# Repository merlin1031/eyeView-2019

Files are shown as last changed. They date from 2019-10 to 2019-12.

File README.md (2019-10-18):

# eyeView-2019 FPV Twin-Mot Plane
eyeView2019 ist ein aus 5mm Depron gebauter, 2-motoriger FPV-Hochdecker der mit 5,8GHz Video-Übertragung den FPV-Flug ermöglicht.
Bei der Konstruktion von eyeView wurde besonders darauf geachtet, dass zu Ausbildungszecken im Bereich CAD möglichst viele Aspekte des eingesetzten CAD-Systems SolidWorks 2019 angewendet werden. Die einzelnen Bauteile werden im Laufe des Projektes dann auf einem LaserCutter und auf einem 3D-Drucker erstellt.

## Idee und Konzept
Angetrieben wird eyeView2019 durch zwei Micro-Brushless-Motoren der FPV-Racer-Drohen Szene. I.d.R. bestiten diese Motoren genügend Kraft um ca. 2KG Schub produzieren zu können. Das dürfte dann bei einem minimalen Abfluggewicht von ca. 500g bis 700g für ein Schubverhälnis von min 1:2 oder noch besser 1:3 sorgen. Zudem sind diese Motoren aktuell zu sehr günstigen Preise überall in den verschiedensten Ausführungen verfügbar.
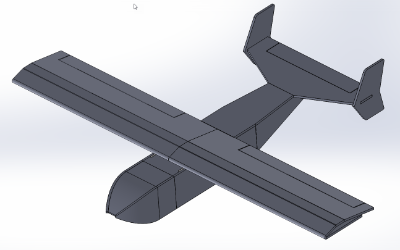
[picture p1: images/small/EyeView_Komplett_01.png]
eyeView2019 - Gesammtansicht Zwischenstand

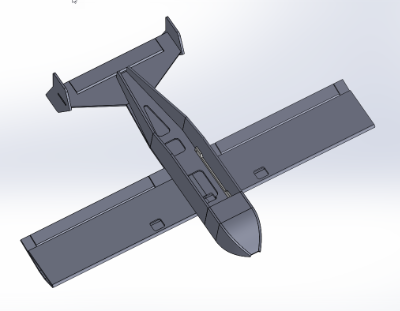
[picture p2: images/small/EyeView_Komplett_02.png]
eyeView2019 - Gesammtansicht Zwischenstand


Die Tragfläche besteht aus insgesamt 4 Einzelteilen, die bei der Montage übergangsweise mit Klebeband zusammengeklebt werden, damit die einzelnen Bauteile zueinander ihre Posisitonierung behalten. Verklebt werden die Deproonteile mit PUR-Leim, der eine Aushärtungszeit von ca. 24h besitzt. Der Vorteil beim Einsatz von PUR-Leim besteht darin, dass dieser mit Hilfe von Feuchtigkeit aufschäumt und somit kleinere Spalte überbrückt. Bei der Verarbeitung von PUR-Leim sind die entsprechenden Sicherheits-Vorschriften einzuhalten.
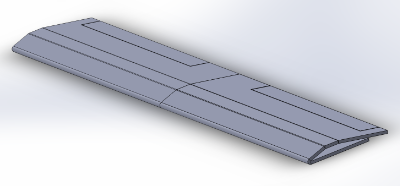
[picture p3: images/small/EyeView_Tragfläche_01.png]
eyeView2019 - Tragfläche


Die Rumpfnase besteht auf vier einzelnen Depron-Platten die leicht über einer Kante in Formbebracht werden. Durch die Formgebung ergibt sich dann eine recht aerodynamische Rumpfnase bei geringem Gewicht. Die Kamera-Halterung für die FPV Kamera wird aus einem 3D gedruckten PLA-Teil bestehen, das in die Rumpfnase aus Depron eingeklebt wird und somit der Kamera etwas mehr Schutz bei einem Crash bietet als reines Depron.
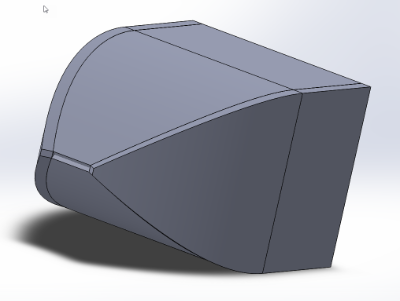
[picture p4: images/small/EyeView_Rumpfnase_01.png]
eyeView2019 - Rumpfnase als Oberflächenteil


## Komponenten und Bauteile
### Rumpf
muss noch beschrieben werden

### Tragfläche

### Höhenleitwerk

### Rumpfnase

### Motor-Gondeln

## weitere Infos

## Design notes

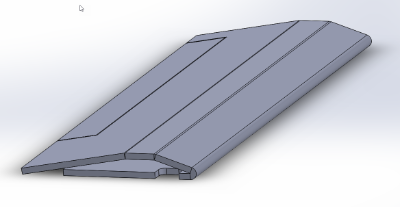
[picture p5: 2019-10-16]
images/small/EyeView_Tragfläche_03.png

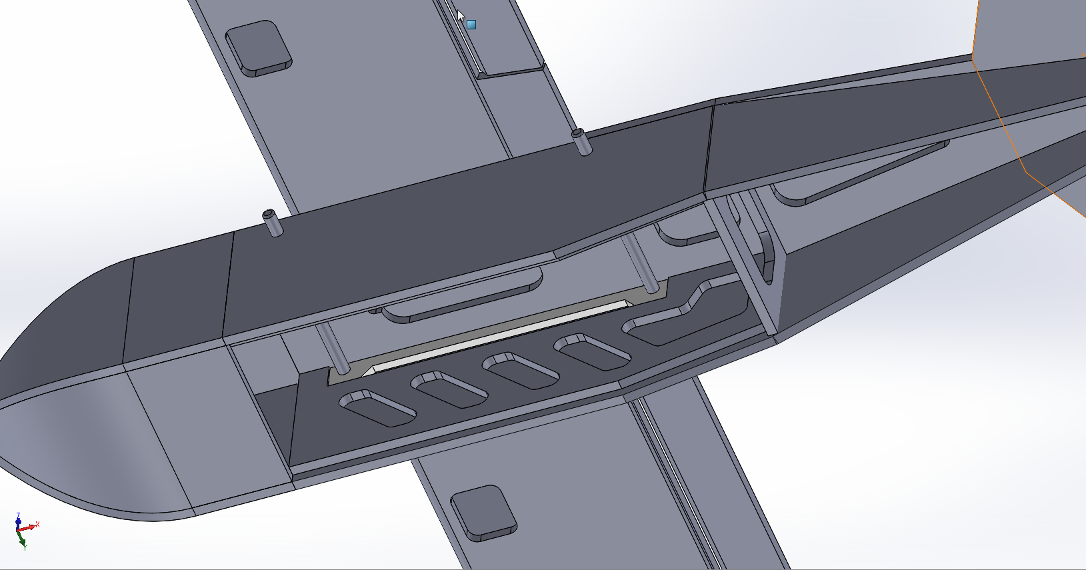
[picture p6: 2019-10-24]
images/EyeView_Rumpf_04.png

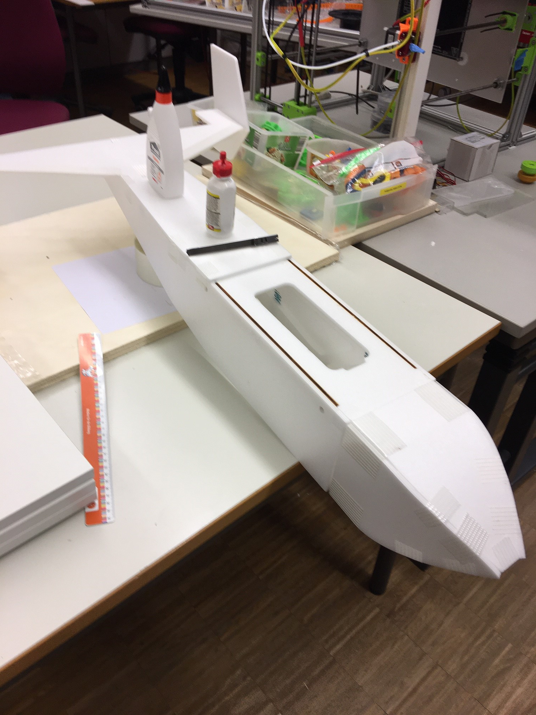
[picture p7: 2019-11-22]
images/Prototyp_04.jpg

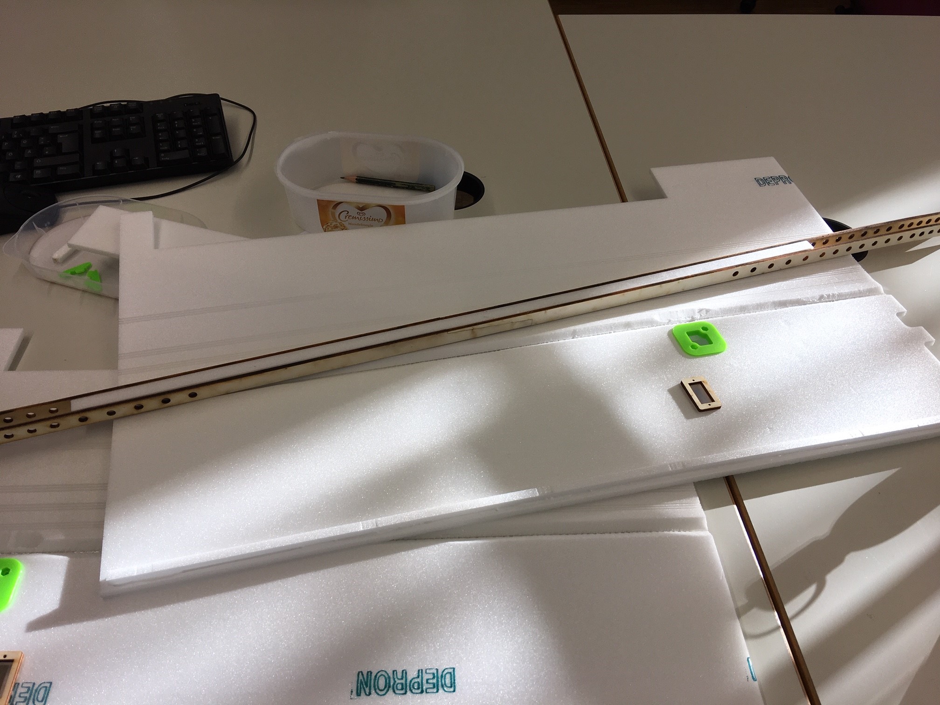
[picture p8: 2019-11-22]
images/Prototyp_07.jpg

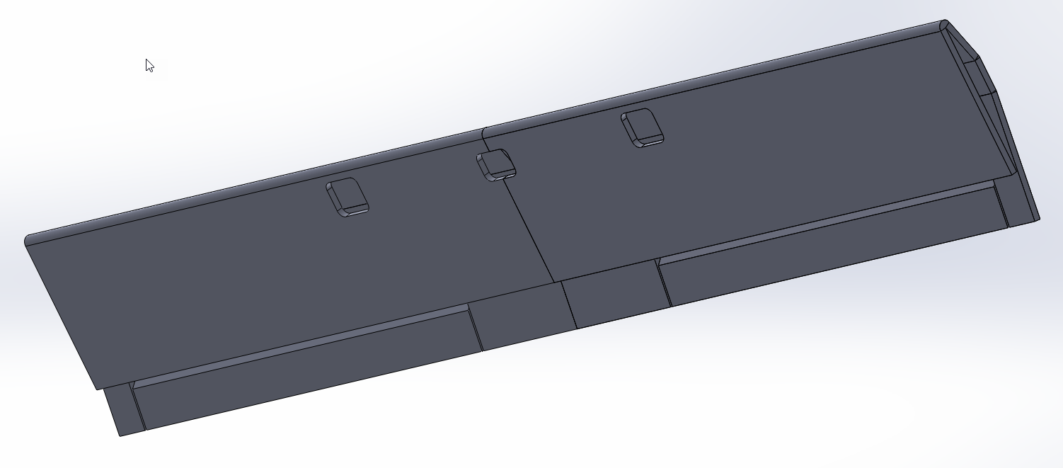
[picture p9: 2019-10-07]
images/EyeView_Tragfläche_02.png

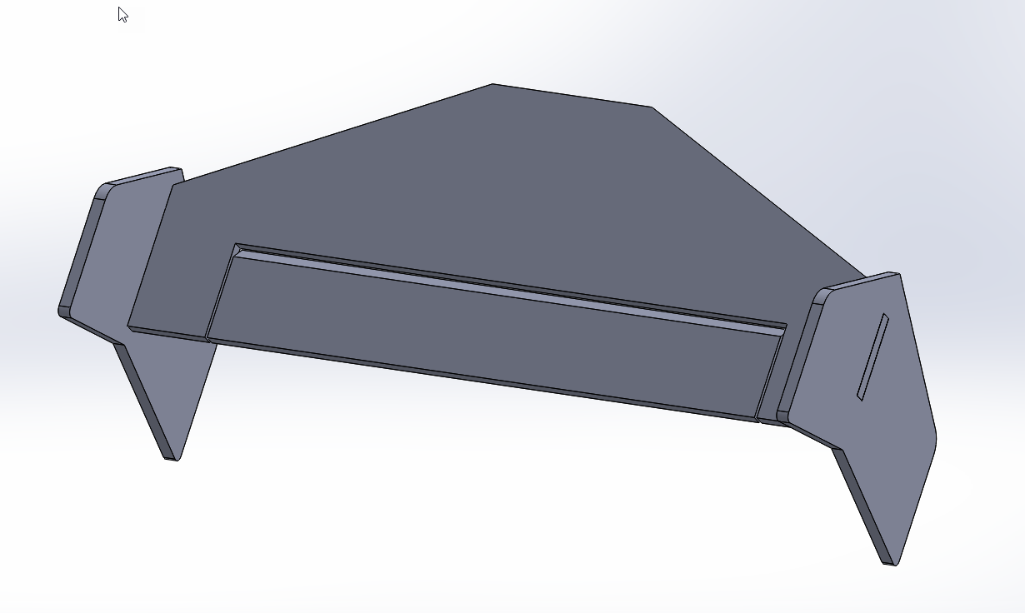
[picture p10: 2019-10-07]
images/EyeView_HL-BG_02.png

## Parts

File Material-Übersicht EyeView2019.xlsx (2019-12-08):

 | Bauteil | Bezeichung / Material | Bezugsquelle | Menge | Einheit | Einzel-Preis | Summe
345.16 €
Modellkosten incl. Elektronic / Antrieb | Depron-Bauteile | Platte 1250x800x6mm | epp-versand | 3 | stk | 6.15 € | 18.45 €
 | Kiefern-Rundstab | 6mm * 200mm | Bauhaus | 2 | stk | 0.35 € | 0.70 €
 | Glasfaser-Gewebeband | PP Filamentband transparent 50mm | Amazon | 8 | m | 0.15 € | 1.20 €
 | Servo 8g Klasse | Torcster Micro Servo NR-62 MG 12g | Natterer-Modellbau | 3 | stk | 11.90 € | 35.70 €
 | Regler | 30A div. Hersteller | z.B. Banggood | 2 | stk | 10.50 € | 21.00 €
 | Motor | 2306 / 2300KV | Banggood | 2 | stk | 10.00 € | 20.00 €
 | Kabel Motor | Silikonkabel AWG12 rot/schwarz | Banggood | 1 | m | 4.60 € | 4.60 €
 | Kabel Servo Querruder | Servokabel JR 3x0,25qmm 5m | Natterer-Modellbau | 0.8 | m | 1.40 € | 1.12 €
 | Kabel Servo Höhenruder | Servokabel JR 3x0,25qmm 5m | Natterer-Modellbau | 0.5 | m | 1.40 € | 0.70 €
 | XT-60 Akkustecker | XT-60 Stecker Paar | Banggood | 2 | stk | 0.65 € | 1.30 €
 | MPX-Stecker Querruder | MPX-Stecker 6Pol (Hochstromstecker MPX) | Natterer-Modellbau | 1 | stk | 1.00 € | 1.00 €
 | Kleber PUR | Ponal Pur 12 Holz-/ PUR-Leim HV 860, Flasche 420 g | Amazon | 100 | g | 0.04 € | 4.00 €
 | Schrumpfschlauch | div. Durchmesser (Akku-Kabel, Servokabel) | Conrad | 0.5 | m | 2.00 € | 1.00 €
 | Empfänger | nach System (MPX / Spektrum / FrSky) | Angebot JugendGruppe | 1 | stk | 30.00 € | 30.00 €
 | Pappelsperrholz | A3 4mm Stärke (evtl. 5-fach Flugzeugsperrholz verwenden) | Bauhaus | 1 | stk | 2.70 € | 2.70 €
 | Gummiringe | elastische Gummibänder lang 130x10mm | Amazon | 4 | stk | 0.30 € | 1.20 €
 | Propeller | DALPROP T5045C Cyclone 5 | Banggood | 2 | stk | 1.25 € | 2.50 € | 147.17 €
Akku | Akku | SLS 3S 1500mAh | Angebot JugendGruppe | 2 | stk | 20.00 € | 40.00 €
 |  |  |  |  |  |  | 0.00 € | 40.00 €
Ausrüstung Versicherung | Sender | nach System (MPX / Spektrum / FrSky) | Angebot JugendGruppe | 1 | stk | 100.00 € | 100.00 €
 | Ladegerät | ToolkitRC M6 DC 150W 10A LCD 2-6S Lipo Battery Smart Balance Charger Discharger | Banggood | 1 | stk | 30.00 € | 30.00 €
 | Netzteil | Leicke Netzteil 60W 12V 5A | Amazon | 1 | stk | 15.99 € | 15.99 €
 | Haftpflichtversicherung | z.B. Jugendbeitrag DMFV (€ 12,00 p/a) | DMFV | 1 | jährlich | 12.00 € | 12.00 €
 |  |  |  |  |  |  | 0.00 € | 157.99 €

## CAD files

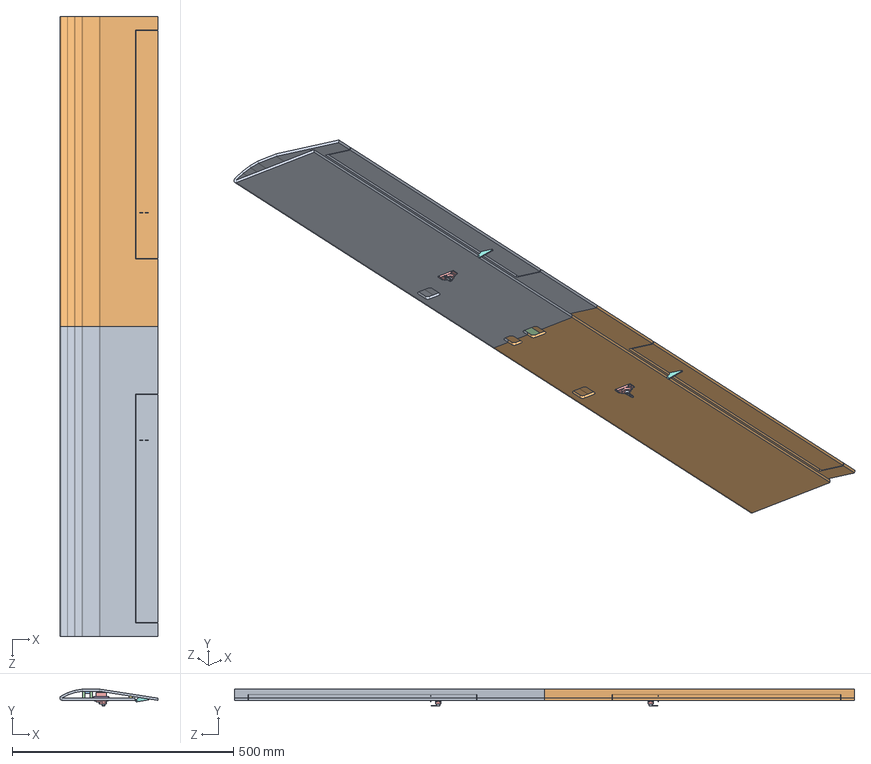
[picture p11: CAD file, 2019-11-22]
CAD/EyeView_BG_Tragfläche.SLDASM
222.4 x 38.0 x 1400.0 mm
EyeView_Tragfläche
EyeView_TragflächeAS
EyeView_Holm_MittelSteg
EyeView_Holm_VerbindungsSteg x 4
EyeView_Servo_8g_Klasse_NewPower-XL-9 x 2
EyeView_ServoEInbaurahmen x 2
SkyView_TragflächeEndleiste x 2
EyeView_RuderAnlenkung x 2
EyeView_ServoHorn_8g_Klasse x 2

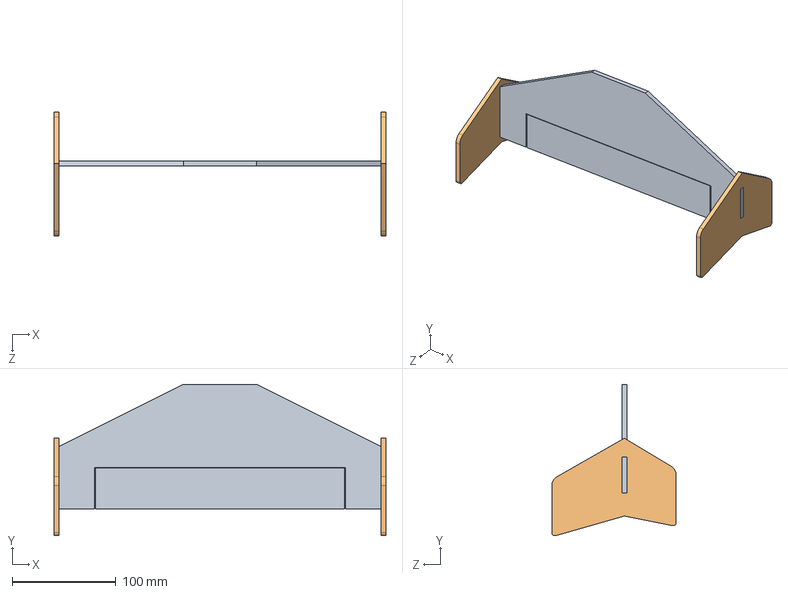
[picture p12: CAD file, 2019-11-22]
CAD/EyeView_BG_Höhenleitwerk.SLDASM
320.0 x 146.0 x 120.0 mm
EyeView_Höhenleitwerk
EyeView_Seitenleitwerk x 2

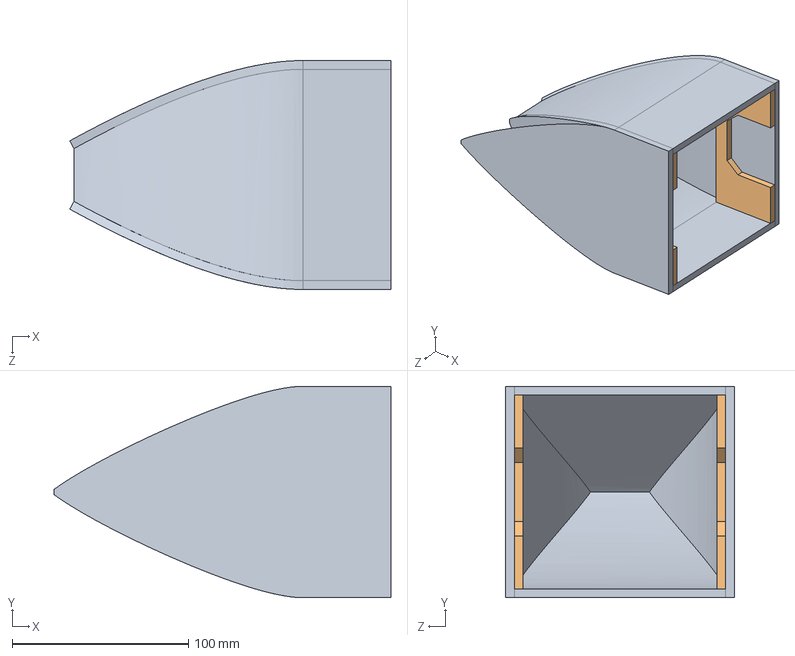
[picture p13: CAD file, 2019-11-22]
CAD/EyeView_BG_Rumpfnase.SLDASM
191.3 x 120.0 x 130.0 mm
EyeView_Rumpfnase
EyeView_NasenAUfdoppler x 2

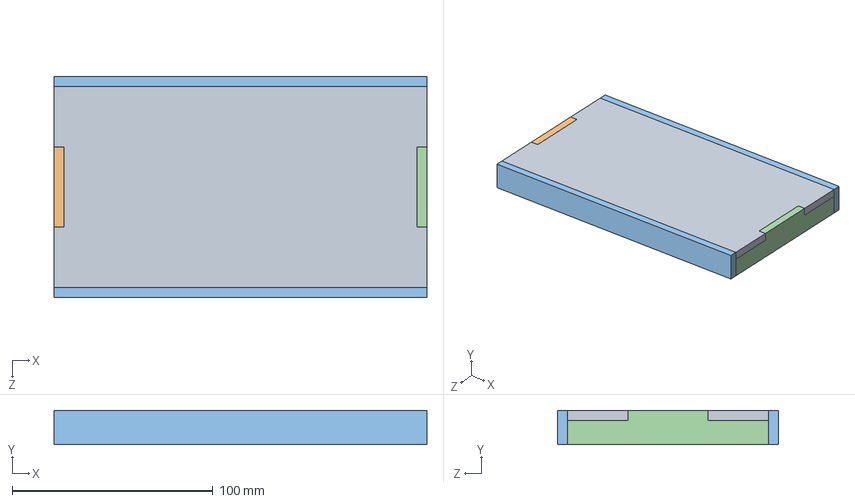
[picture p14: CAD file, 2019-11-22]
CAD/EyeView_BG_AkkuWanne.SLDASM
186.0 x 17.0 x 110.0 mm
EyeView_AkkuWanneBoden x 2
EyeView_AkkuWanneVorderSpant
EyeView_AkkuWanneSeite x 2
EyeView_AkkuWanneEndeSpant

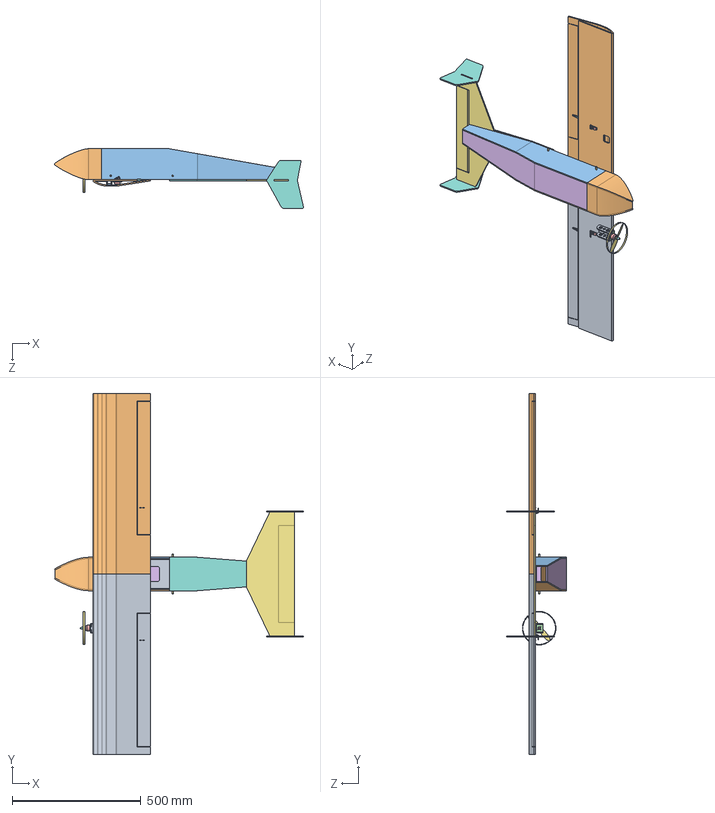
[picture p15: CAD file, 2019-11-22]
CAD/EyeView_BG_Komplett.SLDASM
966.6 x 1400.0 x 231.0 mm
EyeView_Rumpfdeckel
EyeView_RumpfSeiteAussen
EyeView_RumpfSeiteAussenAS
EyeView_Flächenaufdoppler x 2
EyeViewRumpfSeitenDoppler x 2
EyeView_RumpfSpant2
EyeView_GummiBolzen x 2
EyeView_RumpfdeckelTLHL
EyeView_AkkuWanneBoden x 2
EyeView_AkkuWanneVorderSpant
EyeView_AkkuWanneSeite x 2
EyeView_AkkuWanneEndeSpant
EyeView_AkkuBrett
eyeView_Boden
EyeView_Höhenleitwerk
EyeView_Seitenleitwerk x 2
EyeView_Tragfläche
EyeView_TragflächeAS
EyeView_Holm_MittelSteg
EyeView_Holm_VerbindungsSteg x 4
EyeView_Servo_8g_Klasse_NewPower-XL-9 x 2
EyeView_ServoEInbaurahmen x 2
SkyView_TragflächeEndleiste x 2
EyeView_RuderAnlenkung x 2
EyeView_ServoHorn_8g_Klasse x 2
EyeView_Rumpfnase
EyeView_NasenAUfdoppler x 2
EyeView_Firewall
EyeView_T-Motor_1806
EyeView_T-Motor_1806_Propadapter
EyeView_GemFan-5x3_Dummy mit PropKreis
EyeView_T-Motor_1806_Spinner
EyeView_FirewallSeite x 3
EyeView_MotorGondelLagerBlock

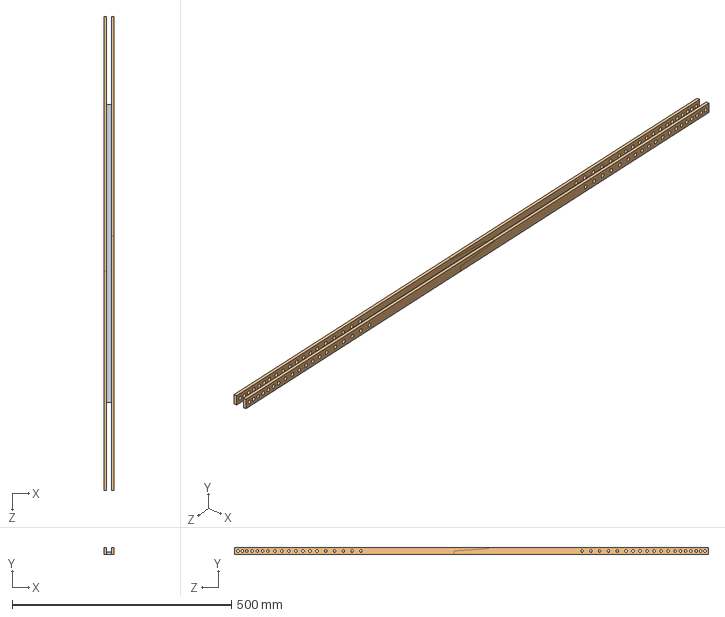
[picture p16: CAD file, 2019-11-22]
CAD/EyeView_BG_Holm.SLDASM
22.0 x 15.5 x 1080.0 mm
EyeView_Holm_MittelSteg
EyeView_Holm_VerbindungsSteg x 4

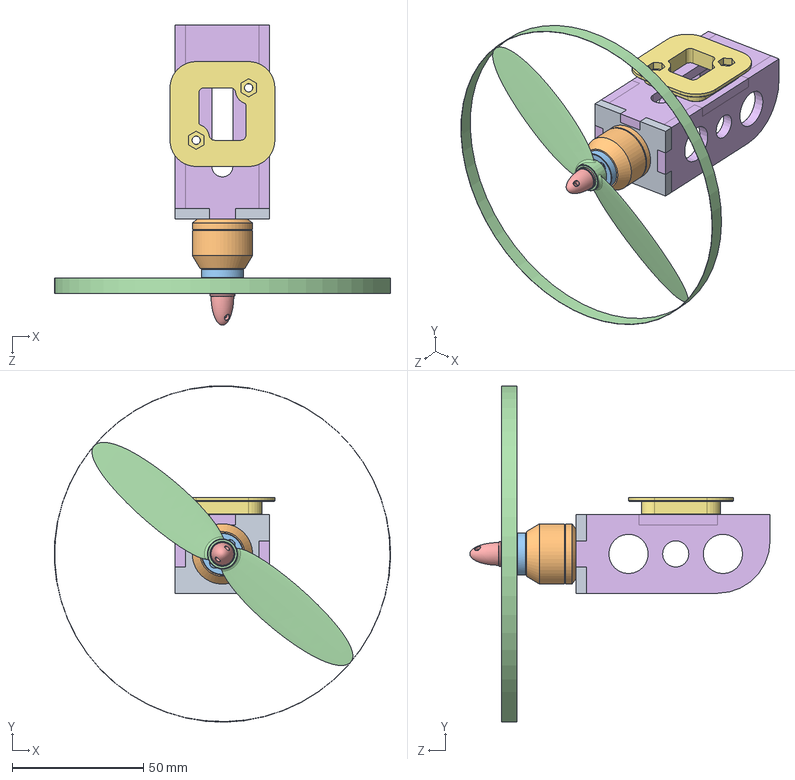
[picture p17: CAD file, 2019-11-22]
CAD/EyeView_BG_MotGondel.SLDASM
128.1 x 128.1 x 114.5 mm
EyeView_Firewall
EyeView_T-Motor_1806
EyeView_T-Motor_1806_Propadapter
EyeView_GemFan-5x3_Dummy mit PropKreis
EyeView_T-Motor_1806_Spinner
EyeView_FirewallSeite x 3
EyeView_MotorGondelLagerBlock

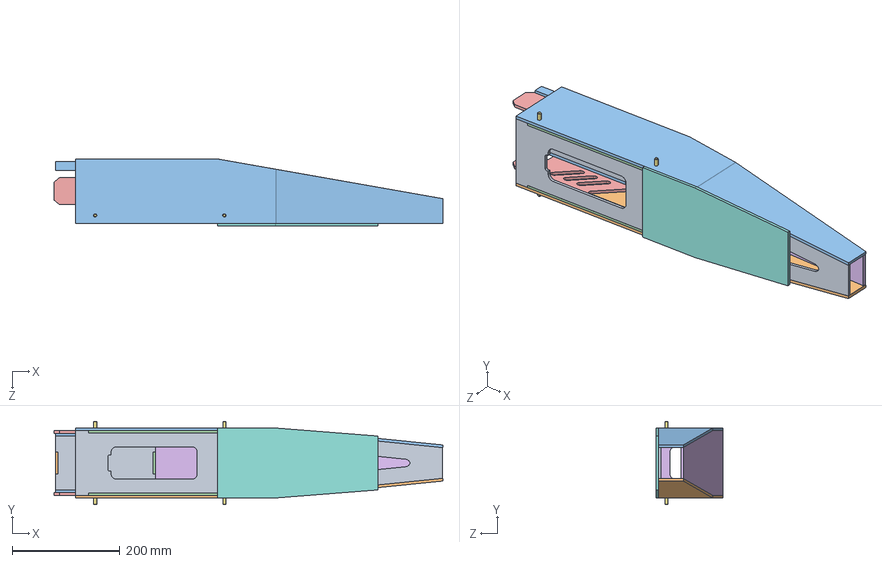
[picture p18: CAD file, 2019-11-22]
CAD/EyeView_BG_Rumpf.SLDASM
722.5 x 155.0 x 125.0 mm
EyeView_Rumpfdeckel
EyeView_RumpfSeiteAussen
EyeView_RumpfSeiteAussenAS
EyeView_Flächenaufdoppler x 2
EyeViewRumpfSeitenDoppler x 2
EyeView_RumpfSpant2
EyeView_GummiBolzen x 2
EyeView_RumpfdeckelTLHL
EyeView_AkkuWanneBoden x 2
EyeView_AkkuWanneVorderSpant
EyeView_AkkuWanneSeite x 2
EyeView_AkkuWanneEndeSpant
EyeView_AkkuBrett
eyeView_Boden

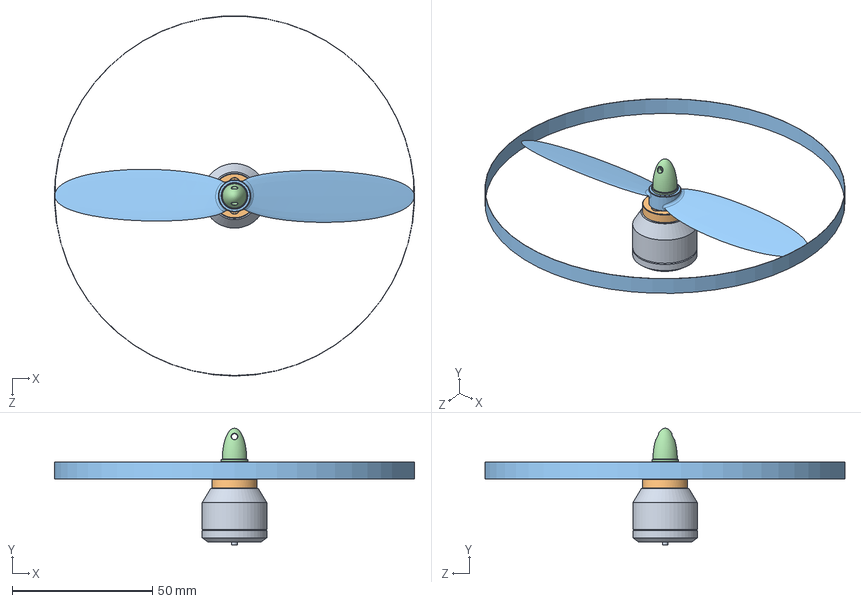
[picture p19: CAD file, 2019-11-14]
CAD/EyeView_BG_Motor_1806Typ.SLDASM
128.1 x 41.5 x 128.1 mm
EyeView_T-Motor_1806
EyeView_T-Motor_1806_Propadapter
EyeView_GemFan-5x3_Dummy mit PropKreis
EyeView_T-Motor_1806_Spinner

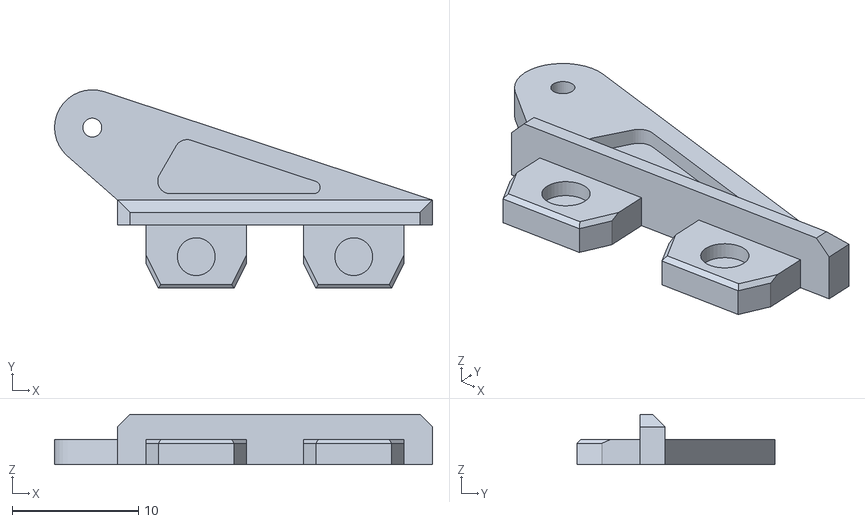
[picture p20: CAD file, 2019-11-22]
CAD/STL-Objekte/EyeView_RuderAnlenkung.STL
30.0 x 15.7 x 4.00

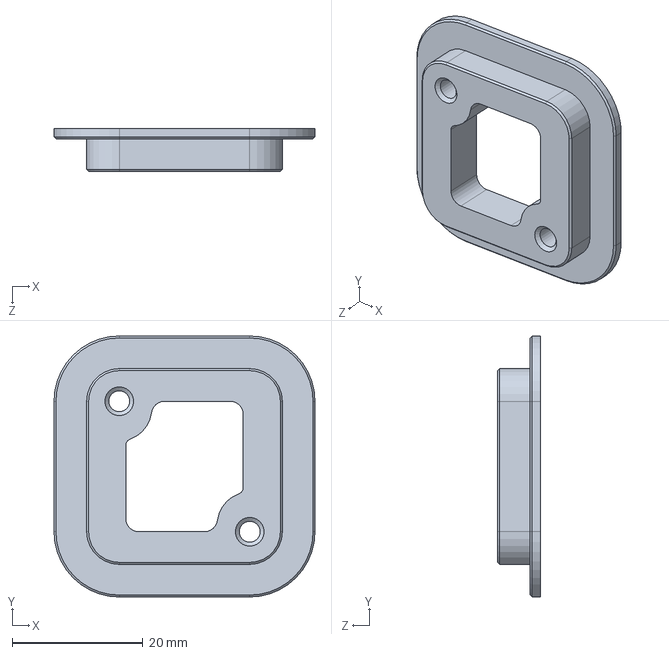
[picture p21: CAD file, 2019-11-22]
CAD/EyeView_MotorGondelLagerBlock.SLDPRT
40.0 x 40.0 x 6.60 mm

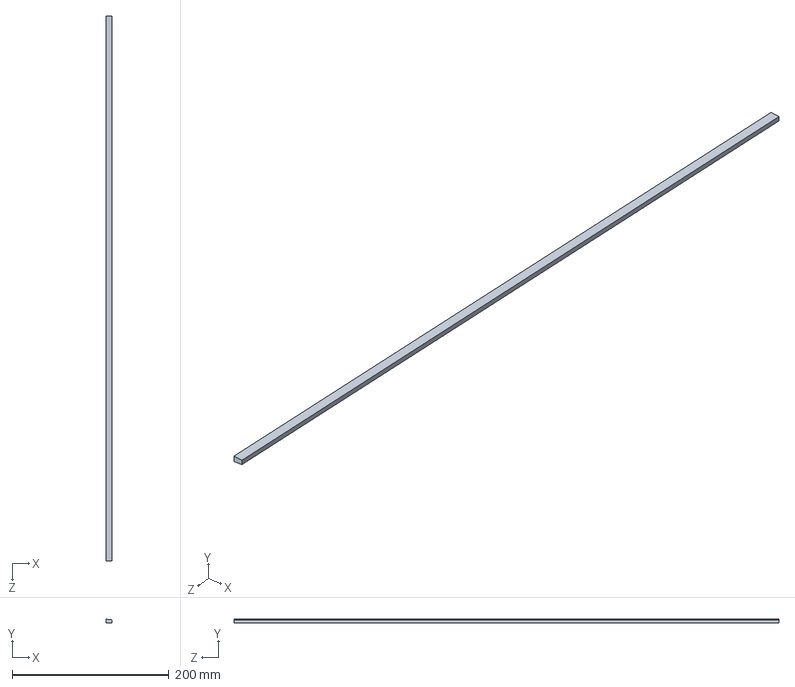
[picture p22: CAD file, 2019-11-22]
CAD/SkyView_TragflächeEndleiste.SLDPRT
8.00 x 5.00 x 695.0 mm

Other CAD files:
CAD/LaserTeile_Var150/04_EyeView_Laserteile_01.DXF
CAD/LaserTeile_Var150/02_EyeView_Laserteile_01.DXF
CAD/STL-Objekte/EyeView_MotorGondelLagerBlock.STL
CAD/LaserTeile_Var150/01_EyeView_Laserteile_01.DXF
CAD/LaserTeile_Var150/03_EyeView_Laserteile_01.DXF
CAD/LaserTeile_Var150/EyeView_Laserteile_01.DXF
CAD/00_01_EyeView_Laserteile_01.DXF
CAD/00_EyeView_Laserteile_01.DXF
CAD/00_eyeview_02-ok.DXF
CAD/01_01_EyeView_Laserteile_01.DXF
CAD/01_EyeView_Laserteile_01.DXF
CAD/01_eyeview_02-ok.DXF
CAD/EyeViewRumpfSeitenDoppler.SLDPRT
CAD/EyeView_AkkuBrett.SLDPRT
CAD/EyeView_AkkuWanneBoden.SLDPRT
CAD/EyeView_AkkuWanneEndeSpant.SLDPRT
CAD/EyeView_AkkuWanneSeite.SLDPRT
CAD/EyeView_AkkuWanneVorderSpant.SLDPRT
CAD/EyeView_Firewall.SLDPRT
CAD/EyeView_FirewallSeite.SLDPRT
CAD/EyeView_Flächenaufdoppler.SLDPRT
CAD/EyeView_GemFan-5x3_Dummy mit PropKreis.SLDPRT
CAD/EyeView_GummiBolzen.SLDPRT
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

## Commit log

2019-10-08 Bilder small und Update readme
2019-10-19 GummiBolzen eingebaut
    Position Tragfläche angepasst, GummiBolzen eingefügt
    [EyeView_BG_Komplett.SLDASM, EyeView_BG_Rumpf.SLDASM, EyeView_Flächenaufdoppler.SLDPRT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]
2019-10-19 FPV Kamera Test
    [EyeView_BG_Komplett.SLDASM, EyeView_RunCam_Eagle.SLDPRT]
2019-10-24 Holm eingefügt
    [EyeView_BG_Holm.SLDASM, EyeView_Holm_MittelSteg.SLDPRT, EyeView_Holm_VerbindungsSteg.SLDPRT]
2019-10-24 Versions Quark grrrrrr
    einige Änderungen im falschen Verzeichnis durchgeführt, müssen hier noch nachgezogen werden.....
    [EyeViewRumpfSeitenDoppler.SLDPRT, EyeView_BG_Komplett.SLDASM, EyeView_BG_Rumpf.SLDASM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]
2019-10-25 Holm eingebaut
    [EyeView_BG_Komplett.SLDASM, EyeView_BG_Tragfläche.SLDASM]
2019-10-25 Servo Lösung und Laserteile
    Servo als Mockup und erste Verswion der Laserteile
    [EyeViewRumpfSeitenDoppler.SLDPRT, EyeView_BG_Tragfläche.SLDASM, EyeView_Laserteile_01.DXF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]
2019-10-25 Anpassungen Maßstab für Export
    Maßstab stimmte nicht beim Export in dxf, da Zeichenblatteinstellungen im falschen Maßstab und in inch.
    [EyeView_Laserteile_01.SLDDRW, EyeView_RumpfSeiteAussenAS.SLDPRT]
2019-10-25 Laserteile in Rhino6
    [EyeView_Laserteile_01.DXF, EyeView_Laserteile_01.SLDDRW, eyeView_Laserteile_01.3dm]
2019-11-14 Erscheinungsbild-Anpassungen / Akkuwanne
    [EyeView_AkkuWanneBoden.SLDPRT, EyeView_AkkuWanneEndeSpant.SLDPRT, EyeView_AkkuWanneSeite.SLDPRT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]
2019-11-14 Firewall und Motorgondeln Rumpfnase
    [EyeView_BG_Komplett.SLDASM, EyeView_BG_MotGondel.SLDASM, EyeView_BG_Motor_1806Typ.SLDASM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]
2019-11-15 Firewall LagerBlock
    [EyeView_FirewallSeite.SLDPRT, EyeView_MotorGondelLagerBlock.SLDPRT]
2019-11-15 MGondelBlock Druck
    [EyeView_MotorGondelLagerBlock.SLDPRT, EyeView_MotorGondelLagerBlock.STL]
2019-11-18 Anpassungen Tragfläche Leitwerk Rumpf
    [EyeView_BG_Höhenleitwerk.SLDASM, EyeView_BG_Komplett.SLDASM, EyeView_BG_Rumpf.SLDASM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]
2019-11-18 Faktor 1,55 und Baugruppen Optimierung
    [EyeViewRumpfSeitenDoppler.SLDPRT, EyeView_AkkuWanneBoden.SLDPRT, EyeView_AkkuWanneEndeSpant.SLDPRT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]
2019-11-21 Zwischenstand Laserteile
    [00_01_EyeView_Laserteile_01.DXF, 00_EyeView_Laserteile_01.DXF, 00_eyeview_02-ok.DXF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]
2019-11-21 3D Druck
    [EyeView_RuderAnlenkung.SLDPRT, EyeView_RuderAnlenkung.STL]
2019-11-21 Fehler Flächenaufdoppler
    [00_EyeView_Laserteile_01.DXF, 01_EyeView_Laserteile_01.DXF, 02_EyeView_Laserteile_01.DXF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]
2019-11-21 Rumpfboden 2
    [EyeView_BG_Komplett.SLDASM, EyeView_BG_Rumpf.SLDASM, EyeView_BG_Rumpfnase.SLDASM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]
2019-11-22 Prototyp gelasert
    [00_EyeView_Laserteile_01.DXF, 01_EyeView_Laserteile_01.DXF, 02_EyeView_Laserteile_01.DXF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]
